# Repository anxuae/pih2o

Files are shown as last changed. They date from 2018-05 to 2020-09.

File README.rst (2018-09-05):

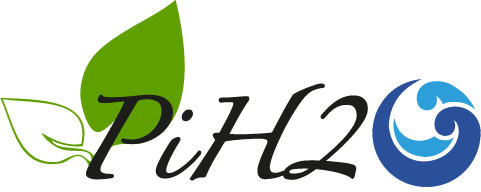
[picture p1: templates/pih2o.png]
PiH2O


The ``pih2o`` project attempts to provide an automatic plant watering application *out-of-the-box*
in pure Python for Raspberry Pi. The watering is triggered for all plants depending on the number
of plants which need water.

Requirements
------------

The requirements listed below are the one used for the development of ``pih2o``, but other
configuration may work fine.

The **pump** can be replaced by an electro valve if the tank water is upper than the plants
(watering by gravity). The number of **soil moisture sensors** can be easily adapted from 1 to 4.
The **transistor** is optional, the sensors can be directly connected to the 5V pin in order
to power them continuously (but it accelerate their corrosion).

Hardware
^^^^^^^^

* 1 Raspberry Pi 2 Model B (or higher)
* 1 pump and its power supply 12V DC (or electro valve)
* 1 to 4 soil moisture sensors (Arduino TE215)
* 1 Analog-to-Digital Converter (ADS1015 or ADS1115 4 Channel I2C)
* 2 transistors NPN (type BC237B)
* 1 transistor PNP high power switch (type BDX34)
* 1 zener diode (type 1N4007)
* 2 resistors of 1.5k Ohm
* 1 resistor of 10k Ohm

Software
^^^^^^^^

* Python ``3.5.3``
* RPi.GPIO ``0.6.3``
* adafruit-ads1x15 ``1.0.2``
* croniter ``0.3.23``
* blinker ``1.4``
* flask ``1.0.2``
* flask-restful ``0.3.6``
* flask-sqlalchemy ``2.3.2``

Install
-------

A brief description on how to set-up a Raspberry Pi to use this software.

1. Download latest Raspbian image and set-up an SD-card. You can follow
   `these instructions <https://www.raspberrypi.org/documentation/installation/installing-images/README.md>`_ .

2. Insert the SD-card into the Raspberry Pi and fire it up. Use the raspi-config tool that is shown
   automatically on the first boot to configure your system (e.g., expand partition, change hostname,
   password, enable SSH, configure to boot into GUI, etc.).

   .. hint:: Don't forget to enable the I2C in raspi-config.

3. Reboot and open a terminal. Install the latest firmware version:

   ::

        $ sudo rpi-update

4. Upgrade all installed software:

   ::

        $ sudo apt-get update
        $ sudo apt-get upgrade

5. Install ``pih2o`` from the `pypi repository <https://pypi.org/project/pih2o/>`_:

   ::

        $ sudo pip3 install pih2o

Run
---

Start the automatic plant watering application using the command::

    $ pih2o

The application acts as a daemon running on the Raspberry Pi. It can be controlled thanks
to an `RESTful API <https://github.com/anxuae/pih2o/blob/master/docs/api.rst>`_.

The ``pih2o`` is scheduled to wake up every given interval, power the soil moisture
sensors and take humidity measurement (or threshold if no analog input available).
Finally the sensors are powered off to extend their lifespan.

.. warning:: Running pih2o in that way use the development server of
    `flask <http://flask.pocoo.org>`_ which is `not suitable in a production
    environment <http://flask.pocoo.org/docs/deploying>`_

Define the record interval
^^^^^^^^^^^^^^^^^^^^^^^^^^

The record interval (i.e. time between each humidity measurement) is defined
in the `Configuration`_ using the `crontab syntax <https://fr.wikipedia.org/wiki/Cron>`_
which is summarized here::

                      ┌───────────── minute (0 - 59)
                      │ ┌───────────── hour (0 - 23)
                      │ │ ┌───────────── day of month (1 - 31)
                      │ │ │ ┌───────────── month (1 - 12)
                      │ │ │ │ ┌───────────── day of week (0 - 6) (Sunday to Saturday)
                      │ │ │ │ │
                      │ │ │ │ │
    record_interval = * * * * *

Pump triggering strategy
^^^^^^^^^^^^^^^^^^^^^^^^

The watering time is defined in the `Configuration`_. The rational to dissociate the pump stop
from the humidity level measured is the soil slow absorption and we want to avoid floor flooding.

Three strategies are defined to detect if watering is required by your plants depending on your
configuration and the number of sensors connected.

* ``[GENERAL][watering_strategy] = majority`` means the pump is triggered if half of sensors
  are triggered.
* ``[GENERAL][watering_strategy] = first`` means the pump is triggered if at least one sensor
  is triggered.
* ``[GENERAL][watering_strategy] = last`` means the pump is triggered if all sensors are
  triggered.

.. note:: if analog channels are available: the sensor is triggered when the humidity read from the AO
          goes below the defined threshold (in %) else if digital channels are available: the sensor
          is triggered if the corresponding DO is set to 1.

Install developing version
--------------------------

If you want to use an unofficial version of the ``pih2o`` application, you need to work from a
clone of this ``git`` repository. Replace the step 5. of the `Install`_ procedure above by the
following actions:

- clone from github ::

   $ git clone https://github.com/anxuae/piH2O.git

- go in the cloned directory ::

   $ cd pih2o

- install ``pih2o`` in editable mode ::

   $ sudo pip3 install -e .

- start the application exactly in the same way as installed from pypi. All modifications performed
  in the cloned repository are taken into account when the application starts.

Configuration
-------------

At the first run, a configuration file is generated in ``~/.config/pih2o/pih2o.cfg``
which permits to configure the behavior of the application. The configuration can be
easily edited using the command::

    $ pih2o --config

The default configuration can be restored with the command (strongly recommended when
upgrading ``pih2o``)::

    $ pih2o --reset

See the `default configuration file <https://github.com/anxuae/pih2o/blob/master/docs/config.rst>`_
for further details.

Circuit diagram
---------------

Soil moisture sensor specification used for this project (the number is up to you but the following
diagram is for up to 4 max):

==================== ==================================
Parameter            Value
==================== ==================================
Input Voltage        3.3 – 5V
Output Voltage       0 – 4.2V
Input Current        35mA
Output Signal        Both Analog (A0) and Digital (D0)
==================== ==================================

Digital sensors
^^^^^^^^^^^^^^^

Here is the diagram for digital sensors (rise to high on dry soil). Depending on the sensor type,
an signal amplifier may be necessary (not represented on this diagram).

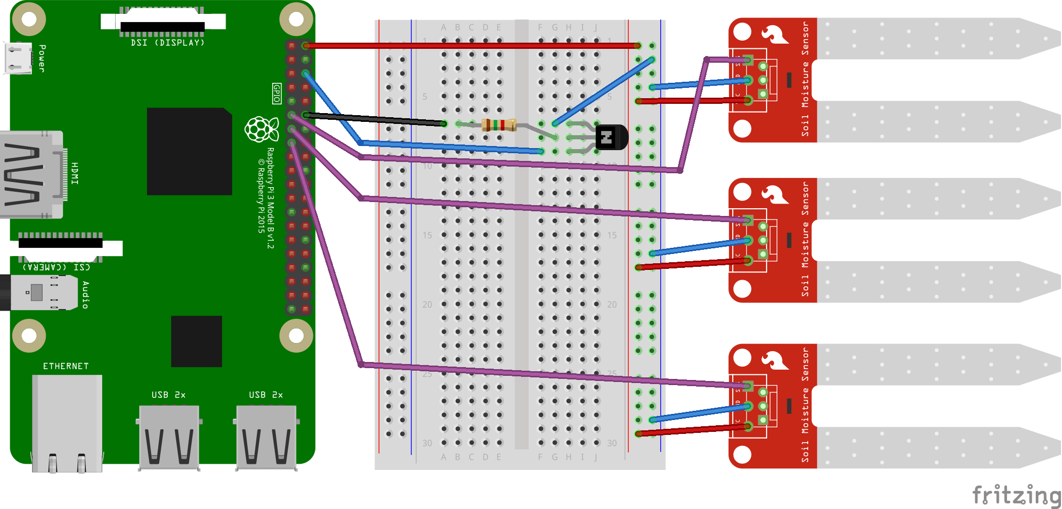
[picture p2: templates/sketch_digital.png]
Electronic sketch for digital sensors


Analog sensors
^^^^^^^^^^^^^^

Here is the diagram for analog sensors connected to an ADC1115 to measure humidity level.

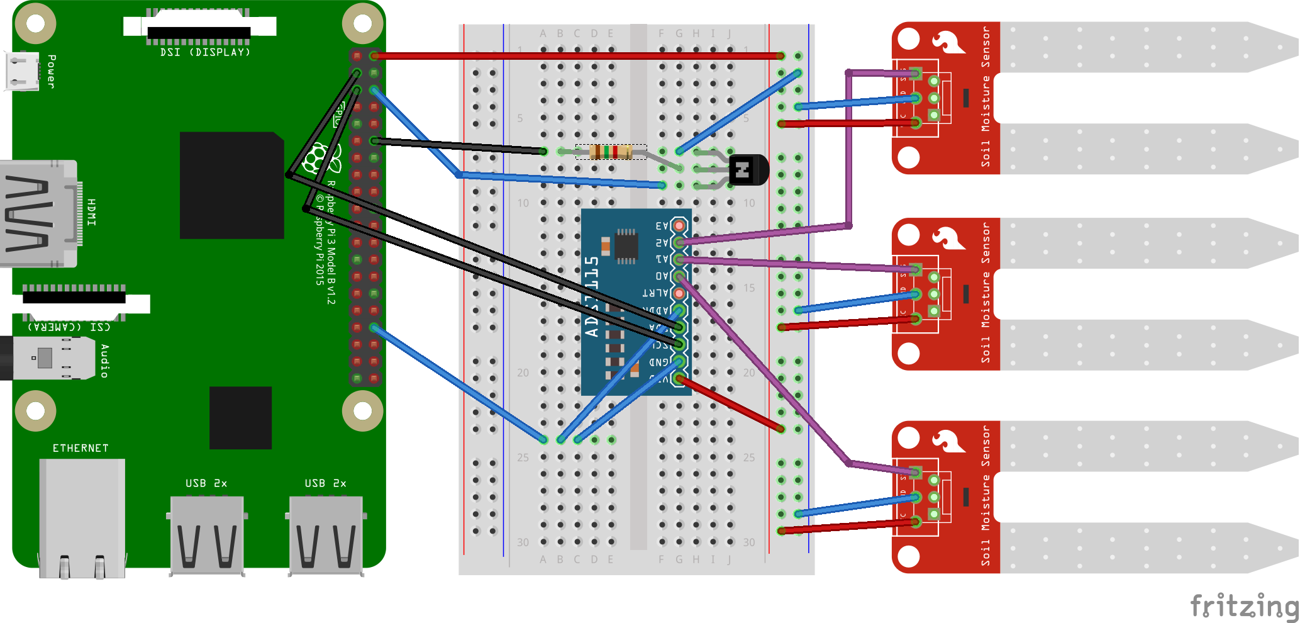
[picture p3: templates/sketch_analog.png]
Electronic sketch for analog sensors


Pump
^^^^

Here is the diagram for the pump (or electro valve). For better understanding the sensors
are not represented here.

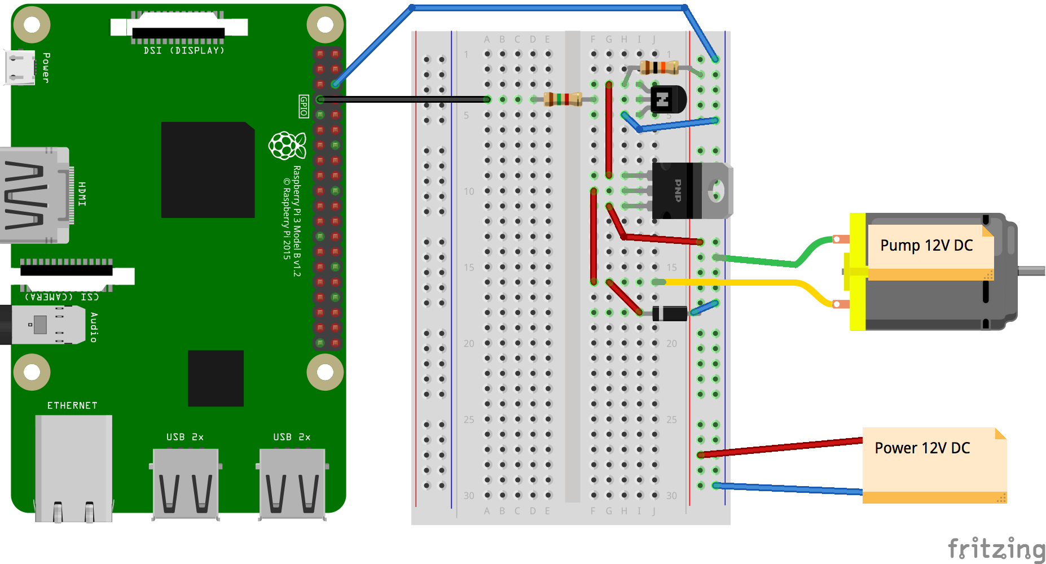
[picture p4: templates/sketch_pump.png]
Electronic sketch for pump


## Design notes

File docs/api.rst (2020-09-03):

RESTful API
-----------

This document describe the API exposed by ``pih2o``. The syntax used is close
to the ``curl`` one, but for readability reasons, not all options are written
and the address is truncated (URL without scheme, domain and port).

It can be necessary to precise the content type of the request in the ``curl``
command by adding the option::

    -H "Content-Type: application/json"
    
Example::
    
    curl -H "Content-Type: application/json" -XGET pi@raspberrypi:/pih2o/api/v1/config

.. contents:: API Contents:

``pih2o``
^^^^^^^^^

**Server information**::

    GET /pih2o

.. code-block:: json

    {
       "name":"pih2o",
       "version":"0.0.0"
    }

``config``
^^^^^^^^^^

**Get entire configuration**::

    GET /pih2o/api/v1/config

.. code-block:: json

    {
       "GENERAL":{
          "autostart":true
       },
       "PUMP":{
          "pin":3,
          "duration":6
       }
    }

**Get all options from a section**::

    GET /pih2o/api/v1/config/<section>

.. code-block:: json

    {
       "autostart":true
    }

**Get value of an option**::

    GET /pih2o/api/v1/config/<section>/<option>

.. code-block:: json

    true

**Update the configuration (partial update supported)**::

    PUT /pih2o/api/v1/config -d '{"<section>": {"<option>": <value>}}'

**Update a section of the configuration (partial update supported)**::

    PUT /pih2o/api/v1/config/<section> -d '{"<option1>": <value1>, <option2>": <value2>}'

**Update value of a specific option**::

    PUT /pih2o/api/v1/config/<section>/<option> -d '<value>'

``pump``
^^^^^^^^

**Start wateing pump for duration defined in the configuration**::

    GET /pih2o/api/v1/pump

**Start wateing pump for 10 seconds**::

    GET /pih2o/api/v1/pump/10

``sensors``
^^^^^^^^^^^

**Get the sensors list IDs (corresponds to the connection pin)**::

    GET /pih2o/api/v1/sensors

.. code-block:: json

    [
        1,
        2,
        3,
        4
    ]

**Get value of the sensor with ID 3**::

    GET /pih2o/api/v1/sensors/3

.. code-block:: json

    {
        "humidity": 33,
        "id": null,
        "record_time": "2018-05-26 10:02:41",
        "sensor": 3,
        "triggered": false
    }

``measurements``
^^^^^^^^^^^^^^^^

**Get the 10 last measurements (by default only 10 measurements are returned for any request)**::

    GET /pih2o/api/v1/measurements

.. code-block:: json

    [
        {
            "humidity": 44.0,
            "id": 10600,
            "record_time": "2018-05-24 20:16:00",
            "sensor": 3,
            "triggered": false
        },

        ...

        {
            "humidity": 26.0,
            "id": 10591,
            ...
        }
    ]

**Get the 100 last measurements**::

    GET /pih2o/api/v1/measurements?lim=100

.. code-block:: json

    [
        {
            "humidity": 44.0,
            "id": 10600,
            "record_time": "2018-05-24 20:16:00",
            "sensor": 3,
            "triggered": false
        },

        ...

        {
            "humidity": 26.0,
            "id": 10591,
            ...
        }
    ]

**Get measurements from a specific sensor**::

    GET /pih2o/api/v1/measurements?sensor=3

.. code-block:: json

    [
        {
            "humidity": 44.0,
            "id": 10600,
            "record_time": "2018-05-24 20:16:00",
            "sensor": 3,
            "triggered": true
        },
        {
            "humidity": 67.0,
            "id": 10530,
            "record_time": "2018-04-24 20:16:00",
            "sensor": 3,
            "triggered": false
        }
    ]

**Get measurements using several query string filters**::

    GET /pih2o/api/v1/measurements?sensor=3&humidity=44.0

.. code-block:: json

    [
        {
            "humidity": 44.0,
            "id": 10600,
            "record_time": "2018-05-24 20:16:00",
            "sensor": 3,
            "triggered": true
        }
    ]

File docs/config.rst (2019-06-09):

Default configuration
---------------------

.. code-block:: ini

    [GENERAL]
    # Start pih2o at Raspberry Pi startup (useful if pih2o not running with a WSGI)
    autostart = False

    # Time between each humidity measurement
    record_interval = 0 19 * * *

    # Percentage under which a sensor is considered as triggered
    humidity_threshold = 20

    # Rules applied to trigger the pump ('first', 'majority' or 'last')
    watering_strategy = majority

    [PUMP]
    # Physical GPIO pin where the pump is connected (or electro-valve)
    pin = 7

    # Watering duration in seconds when the pump is started
    duration = 60

    [SENSOR]
    # Physical GPIO DO-OUT pin use to power on/off the sensors
    power_pin = 12

    # Physical GPIO DO-IN pins to detect threshold exceeded
    digital_pins = (11, 13, 15)

    # ADS1115 channels used to read the humidity level
    analog_pins = (0, 1, 2)

    # Sensor physical range measured with the ADS1115 (from wet to dry)
    analog_range = (10000, 32800)

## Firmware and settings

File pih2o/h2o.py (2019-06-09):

#!/usr/bin/env python3
# -*- coding: utf-8 -*-

"""Pih2o main module.
"""

import sys
import time
import atexit
import threading
import argparse
import logging
from datetime import datetime
from croniter import croniter
import flask
from flask import got_request_exception
from flask_restful import Api
from RPi import GPIO
import pih2o
from pih2o import models
from pih2o.api import ApiConfig, ApiPump, ApiSensors, ApiMeasurements
from pih2o.utils import LOGGER
from pih2o.config import PiConfigParser
from pih2o.controls.pump import Pump
from pih2o.controls.sensor import AnalogHumiditySensor, DigitalHumiditySensor


class PiApplication(object):

    """Plant watering application which is running in background
    of the Flask application which serves the RESTful API.
    """

    def __init__(self, config):
        self._thread = None
        self._stop = threading.Event()
        self.config = config

        LOGGER.debug("Initializing flask instance")
        self.flask_app = flask.Flask(pih2o.__name__)
        self.flask_app.config.from_object('pih2o.config')
        got_request_exception.connect(self.log_exception, self.flask_app)

        @self.flask_app.route('/pih2o')
        def say_hello():
            return flask.jsonify({"name": pih2o.__name__,
                                  "version": pih2o.__version__,
                                  "running": self.is_running()})

        LOGGER.debug("Initializing the database for measurements")
        models.db.init_app(self.flask_app)
        with self.flask_app.app_context():
            models.db.create_all()

        LOGGER.debug("Initializing the RESTful API")
        self.api = Api(self.flask_app, catch_all_404s=True)

        root = '/pih2o/api/v1'
        self.api.add_resource(ApiConfig,
                              root + '/config',
                              root + '/config/<string:section>',
                              root + '/config/<string:section>/<string:key>',
                              endpoint='config', resource_class_args=(config,))
        self.api.add_resource(ApiPump,
                              root + '/pump',
                              root + '/pump/<int:duration>',
                              endpoint='pump', resource_class_args=(self,))
        self.api.add_resource(ApiSensors,
                              root + '/sensors',
                              root + '/sensors/<int:pin>',
                              endpoint='sensors', resource_class_args=(self,))
        self.api.add_resource(ApiMeasurements,
                              root + '/measurements',
                              endpoint='measurements', resource_class_args=(models.db,))

        # The HW connection of the controls
        GPIO.setmode(GPIO.BOARD)  # GPIO in physical pins mode
        self.pump = None
        self.sensors = []
        self._pump_timer = None

        self.init_controls()

        atexit.register(self.shutdown_daemon)

    def log_exception(self, sender, exception, **extra):
        """Log an exception"""
        sender.logger.error('Got exception during processing: %s', exception)

    def init_controls(self):
        """Initializing HW contols.
        """
        self.pump = Pump(self.config.getint("PUMP", "pin"))

        read_pins = self.config.gettyped("SENSOR", "analog_pins")
        if read_pins:
            # Use analog sensors
            sensor_class = AnalogHumiditySensor
        else:
            # Use digital sensors
            read_pins = self.config.gettyped("SENSOR", "digital_pins")
            sensor_class = DigitalHumiditySensor

        if isinstance(read_pins, int):  # May have only one sensor
            read_pins = (read_pins,)

        if not read_pins:
            raise ValueError("Neither analog nor digital sensor defined in the configuration")

        for pin in read_pins:
            self.sensors.append(sensor_class(pin, self.config.gettyped("SENSOR", "power_pin"),
                                             self.config.gettyped('SENSOR', 'analog_range')))

    def is_running(self):
        """Return True if the watering daemon is running.
        """
        if self._thread:
            return self._thread.is_alive()
        return False

    def start_watering(self, duration=None):
        """Start the pump for plant watering.

        :param duration: watering duration in seconds
        :type duration: int
        """
        if not self.pump:
            raise EnvironmentError("The pump is not initialized")
        if not duration:
            duration = self.config.getint("PUMP", "duration")
        self.pump.start()
        self._pump_timer = threading.Timer(duration, self.pump.stop)
        self._pump_timer.daemon = True
        self._pump_timer.start()

    def read_sensors(self, sensor_pin=None):
        """Read values from one or all sensors.

        :param sensor_id: pin of the sensor
        :type sensor_id: int
        """
        if not self.sensors:
            raise EnvironmentError("The sensors are not initialized")

        data = []
        for sensor in self.sensors:
            if sensor_pin is not None and sensor.pin != sensor_pin:
                continue

            if sensor.stype == 'analog':
                humidity = sensor.get_value()
                triggered = humidity <= self.config.getfloat("GENERAL", "humidity_threshold")
            else:
                humidity = 0
                triggered = sensor.get_value()

            measure = models.Measurement(**{'sensor': sensor.pin,
                                            'humidity': humidity,
                                            'triggered': triggered,
                                            'record_time': datetime.now()})

            LOGGER.debug("New measurement: sensor=%s, humidity=%s, triggered=%s",
                         sensor.pin, measure.humidity, measure.triggered)

            data.append(measure)

        for sensor in self.sensors:
            sensor.power_off()

        return data

    def start_daemon(self):
        """Start the watering daemon main loop.
        """
        if self.is_running():
            raise EnvironmentError("Watering daemon is already running")
        self._stop.clear()
        self._thread = threading.Thread(target=self.main_loop)
        self._thread.daemon = True
        self._thread.start()
        LOGGER.debug("Watering daemon started")

    def main_loop(self):
        """Watering daemon loop.
        """
        cron_pattern = self.config.get('GENERAL', 'record_interval')
        if not croniter.is_valid(cron_pattern):
            raise ValueError("Invalid cron pattern '{}'".format(cron_pattern))

        cron = croniter(cron_pattern)
        next_record = cron.get_next()

        while not self._stop.is_set():
            if self._stop.wait(next_record - time.time()):
                break  # Stop requested

            # Calculate next wakeup time
            next_record = cron.get_next()

            # Take a new measurement
            triggered_sensors = []
            untriggered_sensors = []
            with self.flask_app.app_context():

                for measure in self.read_sensors():
                    models.db.session.add(measure)
                    if measure.triggered:
                        LOGGER.info("Sensor on physical pin '%s' is triggered", measure.sensor)
                        triggered_sensors.append(measure)
                    else:
                        untriggered_sensors.append(measure)

                models.db.session.commit()

            # Start the watering if necessary (do nothing if already running)
            strategy = self.config.get('GENERAL', 'watering_strategy')
            if (strategy == 'majority' and float(len(triggered_sensors)) >= float(len(untriggered_sensors))) or \
                    (strategy == 'first' and triggered_sensors) or \
                    (strategy == 'last' and not untriggered_sensors):
                if self.pump.is_running():
                    LOGGER.warning("Skipping watering because pump is already running")
                else:
                    self.pump.start()
                    self._stop.wait(self.config.getint("PUMP", "duration"))
                    self.pump.stop()

    def shutdown_daemon(self):
        """Quit the watering daemon.
        """
        if self._pump_timer:
            self._pump_timer.cancel()

        if self.is_running():
            self._stop.set()
            self._thread.join()
            LOGGER.debug("Watering daemon stopped")

        # To be sure and avoid floor flooding :)
        self.pump.stop()

        GPIO.cleanup()


def create_app(cfgfile="~/.config/pih2o/pih2o.cfg"):
    """Entry point to use with a WSGI server (e.g. gunicorn).
    """
    parser = argparse.ArgumentParser(usage="%(prog)s [options]", description=pih2o.__doc__)

    parser.add_argument('--version', action='version', version=pih2o.__version__,
                        help=u"show program's version number and exit")

    parser.add_argument("--config", action='store_true',
                        help=u"edit the current configuration")

    parser.add_argument("--reset", action='store_true',
                        help=u"restore the default configuration")

    parser.add_argument("--log", default=None,
                        help=u"save console output to the given file")

    group = parser.add_mutually_exclusive_group()
    group.add_argument("-v", "--verbose", dest='logging', action='store_const', const=logging.DEBUG,
                       help=u"report more information about operations", default=logging.INFO)
    group.add_argument("-q", "--quiet", dest='logging', action='store_const', const=logging.WARNING,
                       help=u"report only errors and warnings", default=logging.INFO)

    options, _args = parser.parse_known_args()

    logging.basicConfig(filename=options.log, filemode='w',
                        format='[ %(levelname)-8s] %(name)-18s: %(message)s', level=options.logging)

    config = PiConfigParser(cfgfile, options.reset)

    if options.config:
        LOGGER.info("Editing the automatic plant watering configuration...")
        config.open_editor()
        sys.exit(0)
    elif not options.reset:
        LOGGER.info("Starting the automatic plant watering application...")
        app = PiApplication(config)
        app.start_daemon()
        return app.flask_app  # Return the WSGI application
    else:
        sys.exit(0)


def main():
    """Entry point in case of 'direct' run (without WSGI server)
    """
    app = create_app()
    app.run(use_reloader=False)  # Dont want to start the daemon 2 times


if __name__ == '__main__':
    main()

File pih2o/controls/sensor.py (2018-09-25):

# -*- coding: utf-8 -*-

"""Sensors management.
"""

import time
import threading
from RPi import GPIO
import Adafruit_ADS1x15
from pih2o.utils import LOGGER


class HumiditySensor(object):

    """
    Base class for sensors.
    """

    stype = None
    power_state = {}  # Keep power pins of all sensors to mutualize on/off

    def __init__(self, pin, power_pin=0, analog_range=None):
        self.pin = pin
        self.power_pin = power_pin  # 0 means do not manage the power
        self.analog_range = analog_range or []
        self._lock = threading.Lock()

        if self.power_pin and self.power_state.get(self.power_pin) is None:
            GPIO.setup(self.power_pin, GPIO.OUT)  # Never been setup
            self.power_state[self.power_pin] = False

    def power_on(self):
        """Power on the sensor.
        """
        if self.power_pin and not self.power_state[self.power_pin]:
            GPIO.output(self.power_pin, GPIO.HIGH)
            time.sleep(3)  # Make sure the sensor is powered and ready
            self.power_state[self.power_pin] = True

    def get_value(self):
        """Return the sensor value.
        The sensor is automatically powered on if necessary.
        """
        with self._lock:
            self.power_on()
            return self._read()

    def power_off(self):
        """Power off the sensor.
        """
        if self.power_pin and self.power_state[self.power_pin]:
            GPIO.output(self.power_pin, GPIO.LOW)
            self.power_state[self.power_pin] = False

    def _read(self):
        raise NotImplementedError


class DigitalHumiditySensor(HumiditySensor):

    stype = 'digital'

    def __init__(self, *args, **kwargs):
        HumiditySensor.__init__(self, *args, **kwargs)
        GPIO.setup(self.pin, GPIO.IN)

    def _read(self):
        """Return True if the sensor has detected a low humidity level.
        """
        return GPIO.input(self.pin) == GPIO.HIGH


class AnalogHumiditySensor(HumiditySensor):

    adc = None
    stype = 'analog'

    def __init__(self, *args, **kwargs):
        HumiditySensor.__init__(self, *args, **kwargs)

        if not AnalogHumiditySensor.adc:
            # Ensure uniq connection to ADS1x15
            AnalogHumiditySensor.adc = Adafruit_ADS1x15.ADS1115()

    def _read(self):
        """Return the humidity level (in %) measured by the sensor.
        """
        # Choose gain 1 because the sensor range is +/-4.096V
        value = self.adc.read_adc(self.pin, gain=1)
        if value < min(self.analog_range) or value > max(self.analog_range):
            LOGGER.warning("Sensor %s value '%s' is outside the defined range %s", self.pin, value, self.analog_range)
        return 100 - (value - min(self.analog_range)) * 100. / (max(self.analog_range) - min(self.analog_range))

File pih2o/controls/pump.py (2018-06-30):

# -*- coding: utf-8 -*-

"""Pih2o pump / electro-valve management.
"""

import threading
from RPi import GPIO
from pih2o.utils import LOGGER


class Pump(object):

    def __init__(self, pin):
        self._running = threading.Event()

        self.pin = pin
        GPIO.setup(pin, GPIO.OUT)
        GPIO.output(self.pin, GPIO.LOW)

    def is_running(self):
        """
        Return True if the pump is started.
        """
        return self._running.is_set()

    def start(self):
        """
        Start the pump.
        """
        if self.is_running():
            # Avoid starting several times to prevent concurent access
            raise IOError("Watering is already started")

        LOGGER.info("Starting pump (physical pin %s)", self.pin)
        GPIO.output(self.pin, GPIO.HIGH)
        self._running.set()

    def stop(self):
        """
        Stop the pump.
        """
        LOGGER.info("Stoping pump (physical pin %s)", self.pin)
        GPIO.output(self.pin, GPIO.LOW)
        self._running.clear()

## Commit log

2018-05-16 First commit with pseudo architecture
    [sketch.fzz]
2018-05-21 Create thread for measurements and add dep to croniter
2018-05-24 API for measurements accepts query string filters
2018-05-25 Add API for stating watering pump
2018-05-25 Add classes for pump and sensors
2018-05-26 First working version with digital sensors
2018-05-27 Fix power management of sensors and update doc
    [config.py, h2o.py, sensor.py]
2018-05-27 Add circuit diagrams
    [sketch.fzz, sketch_analog.fzz, sketch_digital.fzz]
2018-05-29 Add parameter to choose watering strategy
    [sketch_analog.fzz, sketch_digital.fzz]
2018-06-05 Small fixes on pins and measurements
    [api.py, config.py, h2o.py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]
2018-06-05 Add sketch for the pump
    [sketch_pump.fzz]
2018-06-24 Update electronic sketchs
    [sketch_analog.fzz, sketch_digital.fzz, sketch_pump.fzz]
2018-06-30 Force stop the pump at startup
2018-09-25 Create connection to ADS1x15 at first sensor created
2018-09-26 Fix run without WSGI server
    [h2o.py]
2019-06-10 API: add error if invalid sensor ID given
    [api.py]
